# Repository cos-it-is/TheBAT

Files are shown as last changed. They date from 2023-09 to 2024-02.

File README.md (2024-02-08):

# Welcome to The B.A.T - A Bitcoin Lightning ATM! 

This repository contains the instructions for building and deploying your very own B.A.T Bitcoin Lightning ATM.

Support the project or buy one here: https://geyser.fund/project/thebatlightningatm or https://satsbat.com 🦇

Support me here: https://www.buymeacoffee.com/cutthepretence 🍺

Join the support group here: https://t.me/BitcoinAutoTeller

====



The B.A.T, short for Bitcoin Auto Teller directly integrates with https://lnbits.com as a funding wallet. 
It is the first highly functional Bitcoin Lightning ATM to incorporate NFC withdrawls that support LNURL, LN Address and [Boltcard](https://www.boltcard.org/ "Boltcard"). It has many features, including thermal printer, NFC withdrawl, and Over-The-Air (OTA) update capability, a large screen and enhanced user customisation options. The B.A.T is designed to sit in between a hobbyists dream and commercial environment.
It was born from a vision to creatly a very useable, small and portable ATM that can spark Bitcoin circular economies anywhere. 
It can be taken to events, markets, shops, parties. All you need is a power supply (plug or battery) and a wifi connection (for some options such as NFC).
It does however, work completely offline.
The ATM also functions as a straight paper Gift voucher dispenser, adding a completely secondary and unique function.



## Trademark

"The BAT" is a trademark. You are welcome to hack, fork, build, and use the source code and instructions found in this repository. However, the right to use the name "The BAT" or logo with any products or services is withheld and reserved for the trademark owner. Please be respectful and utilise your own logo/brand.

The BAT is based on the [FOSSA](https://github.com/lnbits/fossa "FOSSA") by Ben Arc.



====

# Components:

Before starting, please gather the following components that will be required for this project:

12V 3A DC adapter (Power Source) such as [THIS](https://www.ebay.co.uk/itm/225019408019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 "THIS")

12V DC adapter (Power Source) such as [THIS](https://www.ebay.co.uk/itm/225019408019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 "THIS")

12V/5V converter such as [THIS](https://www.ebay.co.uk/itm/193727621572 "THIS")

12V TTL Thermal Printer (You also need the USB to serial cable for uploading the Logo) [THIS](https://www.aliexpress.com/item/4001275848142.html?channel=twinner "THIS")

NV10 USB+ Note acceptor [THIS](https://www.innovative-technology.com/products/products-main/127-nv10-usb "THIS")

DG600F Coin acceptor [THIS](https://www.aliexpress.com/item/32951358676.html?channel=twinner "THIS")

ZX7D00CE01 7-inch screen with integrated ESP32-S3 (You also need the tool for burning) - [THIS](https://www.aliexpress.com/item/1005005000593458.html?spm=a2g0o.order_list.order_list_main.99.4f051802XMsYg2 "THIS")

Momentary 3.3v button (with a harness) such as [THIS](https://www.ebay.co.uk/itm/255737525408 "THIS")

Power 12v button (with a harness) such as [THIS](https://www.ebay.co.uk/itm/255737525408 "THIS")

5.5mm x 2.1mm Female Male DC Power Plug Adapter such as [THIS](https://www.aliexpress.com/item/32990194795.html?channel=twinner "THIS")

5.1mm X 2.1mm female power connector such as [THIS](https://www.aliexpress.com/item/1005003494724471.html?channel=twinner "THIS")

5.1 X 2.1mm Male to Female dual splitter such as [THIS](https://www.aliexpress.com/item/4000552846445.html?channel=twinner "THIS")

HW-307 Relay module or similar such as [THIS](https://www.ebay.co.uk/itm/225559844989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 "THIS")

Coin Acceptor LED Surround such as [THIS](https://www.aliexpress.com/item/1005002995360644.html?channel=twinner "THIS")

NV10 Host Cable - needed to change currency datasets or custom options on the acceptor [THIS](https://innovative-technology.com/shop/cables/nv9-nv10-usb-host-cable-detail "THIS") 

Coin Acceptor LED Surround such as [THIS](https://www.aliexpress.com/item/1005002995360644.html?channel=twinner  "THIS")

PN532 NFC Board (Set in I2C Mode using switches on board) such as [THIS](https://www.amazon.co.uk/HiLetgo-PN532-Module-Communication-Android/dp/B01I1J17LC  "THIS")

====

## Programming the Thermal Printer:

Start by downloading the printer setting software available [THIS](https://www.hsprinter.com/?m=common&a=down&name=639a91a94e329.zip&g=e "THIS") .

• First, you need to ensure that the printer is set to a 19200 baud rate.

• Now, open the printer setting software and navigate to the "Upload" section.

• Select your own printer_logo.bmp file for upload. This should be in greyscale and around 270x270 pixels.

• Proceed to upload the "printer_logo.bmp" file to your thermal printer.

Remember, it is crucial to use the precisely labeled "printer_logo.bmp" file and to set the printer to the 19200 baud rate for successful functioning.

## Programming The DG600F Coin Acceptor:

• Start by holding down the "A" button. Keep it pressed.

• While still pressing the "A" button, press the "A" button again and then hit the "B" button. Do this for the specific coin you want to program (for instance, 5p).

• Continue pressing the buttons for the designated coin until you hear a beep. This usually happens after 20 presses. For accuracy, it is best to use a variety of the same coin.

• Repeat steps 1-3 for all six coins that you want to program.

• Now, press and hold the "B" button, then press the "A" button to switch to the A2 setting. If not sure, the default setting is A1.

• Follow this configuration: Set A2 to 02. Set A3, A4, and A5 to 01.

• Finally, press and hold the "A" button to exit the programming mode.

There are instructions in the manual and many youtube videos of this process available.

## Programming the NV10 USB+ Note Acceptor:

• Download the Validator Manager and Drivers suitable for your specific currency from the Innovative Technologies website (Create a free account).

• Install and plug the cable of the NV10 USB+ into your PC using the host cable cable for programming

• Navigate to your device manager and ensure that your PC detects the connected NV10 USB+ using the instructions in the manual.

• Next, open the Validator Manager software and locate the programming option. Select it.

• In this section, choose the 'bv1' file to program the device.

• Modify the user mode to 'advanced' setting for additional features.

• In the interface section, set the parameter to 'SIO'.

• Now, enable the 'Credit card rejection' option to ensure the machine doesn't process invalid entries.

• Once all changes are completed, ensure to save and apply these new parameters.

## Programming the 7-inch Screen with Integrated ESP32S3 using Arduino:

• Begin by launching your Arduino IDE.

• Connect integrated screen to your PC and install relevant drivers and arduino libraries.

• Navigate to the 'Tools' tab on the menu bar.

• In the dropdown menu, select the options as shown in the image provided:



Alternatively, use a buring tool and the .BIN file provided in releases to install the firmware.

# How to build:
• Connect the devices together as per the wiring diagram. You can use Dupont wires or for the board, you can use a 2x40 (40 pin) IDC connector to breakout the pins. This is a 2mm pitch (not common 2.54mm)

| Terminal Pin | GPIO | Description |
|---|---|---|
| 26 | 40 | Note TXB |
| 27 | 4 | Printer TXP |
| 29 | 1 | Button |
| 23 | 20 | Coin Inhibit |
| 25 | 41 | Note RXB |
| 28 | 42 | Printer RXP |
| 24 | 19 | Coin RXC |
| 30 | 2 | Relay |
| 31 | 47 | NFC - SCL |
| 32 | 48 | NFC - SDA |
| 2 | N/A  | Relay 5v |
| 6 | N/A  | Relay GND |
| 3 | N/A  | Button 3v |
| 5 | N/A  | Button GND |
| 1 | N/A  | NFC 5v |

# How to use:

## Booting into Configuration Mode:
When you want to configure your B.A.T. device, you'll need to launch the access point. To do this, press the boot button on the burner cable during boot. The access point will have a name similar to "The B.A.T - {mac address}".

Once you've connected to the access point, you can begin setting up the device.

This can sometimes be an issue when using OTA updates. It is best (on android at least) I have found using edge browser to perform OTA updates.

## Configuration Options:

Network and wallet configuration, You can change several parameters:

## General Options:

- Access point password: Choose a password to secure your device's access point. Detault is 'thebatatm'
- LNURLDevice string: Set the connection string for funding. This can be from lnbits.com or self-hosted.
- Live rate API URL: Set an API endpoint for retrieving live rates. e.g., https://legend.lnbits.com/lnurlp/api/v1/rate/GBP.
- Wallet endpoint URL: Set the endpoint URL for wallet actions. e.g., https://legend.lnbits.com/api/v1/wallet.
- API Key: Input your API Key, such as 69f5a4afe7834ddsj3jd7dj4f44cd82.
- Screen Brightness: Set to High, Medium or Low.

## Acceptor and Fiat Settings:

- Enable or disable accepting notes or coins.
- Set coin and bill values for the acceptors.
- Set a maximum deposit value for each transaction.
- Set a fee rate.
- You can set a redemption period for each transaction when the thermal printer is in use.

## Custom Options:

- Turn off/on the LED surround for the coin acceptor.
- Enable/disable displaying the live rate. (Wifi connection required)
- Set a balance check after each transaction. (Wifi connection required)

## Withdrawl Settings:
- Set the output display options of the transaction QR codes – it could be the screen, print, or both.
- You can decide to display Bitcoin quotes or jokes on each receipt – it would be selected randomly each time.
- You can set a URL of your website or LNBits install URL (And other information you like) that prints on the receipt for promotional purposes.
- The maximum number of receipts that can be printed on the thermal printer can be set.
- Set in ATM or Gift voucher modes. ATM acts like an ATM, but Gift voucher acts like a voucher dispenser, printing to receipt only and adding different information to the receipt.
- Enable/Disable NFC withdrawls. (Wifi connection required)
- Withdrawl period timeout for transaction (with backup receipt printing if needed)

## Network Time Protovol (NTP) Settings:

- Configure your timezone, NTP server, and sync intervals for accurate timestamps on printed receipts. (Wifi connection required)
- A time offset can be set for regions observing daylight saving.

## Display Settings:

- Change screen brightness
- Set the color mode of your display: default grafitti, stealth black and white, or set your custom color options.

## Translation Settings:

- Set the default and second language (with string translations) for your device. A button press when the ATM is in use will change the language.

## Updating Firmware:
- The B.A.T device allows firmware updates via OTA using .BIN files. To apply a new firmware update, navigate to the Update section in the access point, and proceed to flash the new release of the firmware.

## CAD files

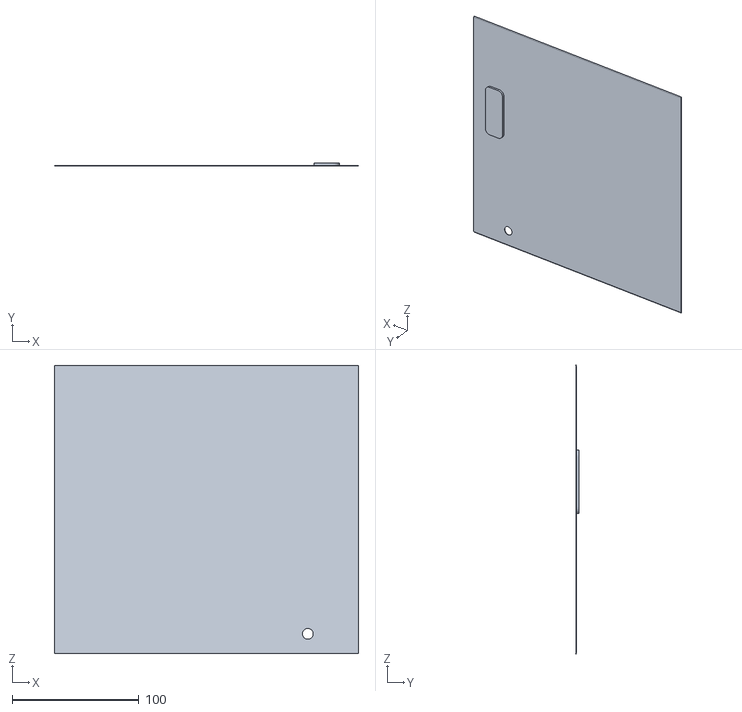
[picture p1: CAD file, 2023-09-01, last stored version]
3D Print Cases/Block/Block Door.stl
240.0 x 2.47 x 227.6

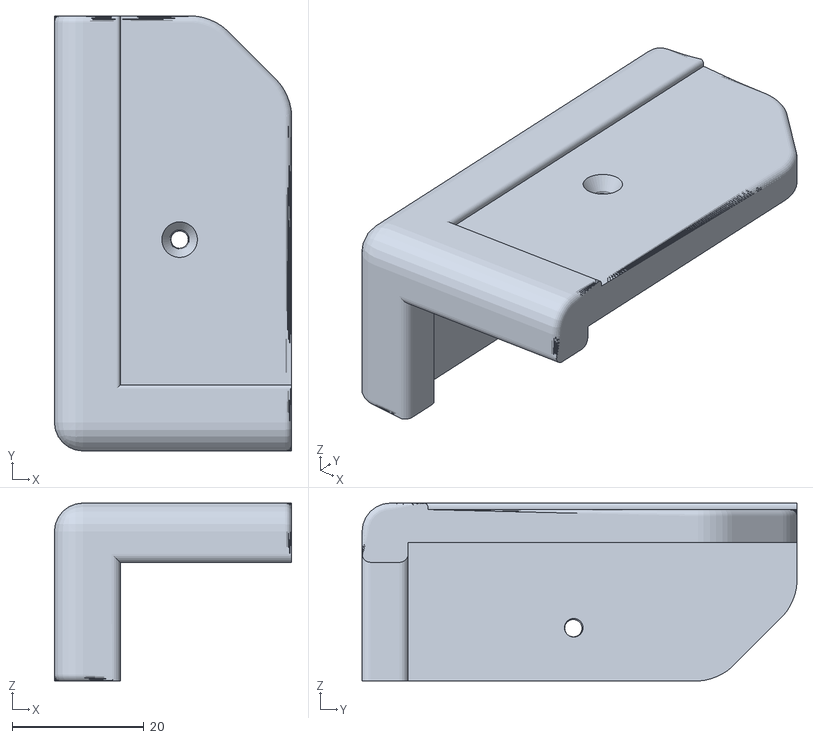
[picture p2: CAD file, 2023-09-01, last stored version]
3D Print Cases/Common/R corner.stl
36.0 x 66.0 x 27.0

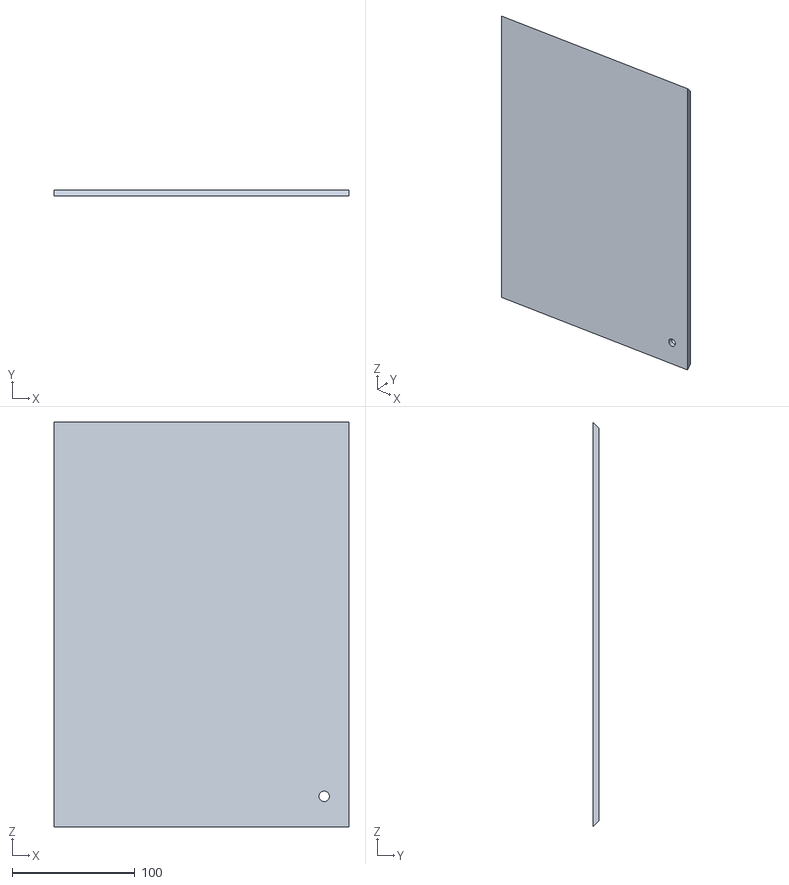
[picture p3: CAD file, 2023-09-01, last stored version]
3D Print Cases/Moon/Moon Door.stl
240.0 x 5.00 x 330.0

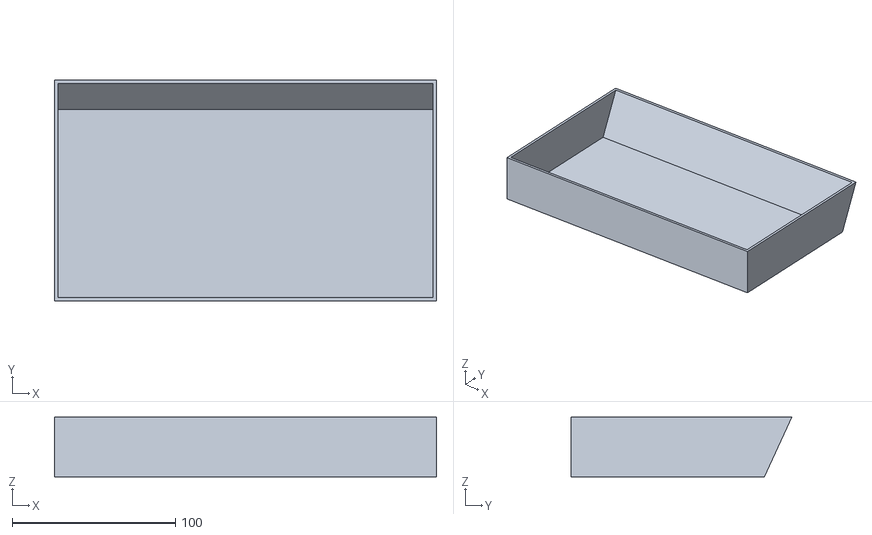
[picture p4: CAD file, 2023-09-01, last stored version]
3D Print Cases/Block/Block Tray.stl
234.0 x 135.2 x 36.5

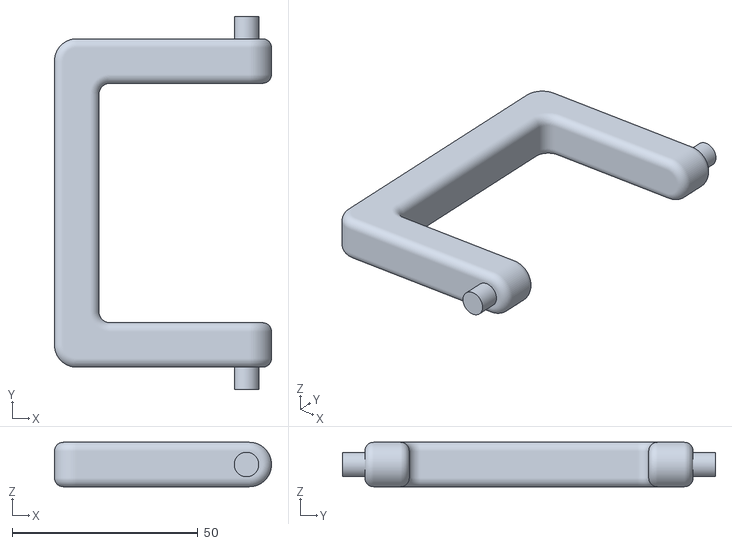
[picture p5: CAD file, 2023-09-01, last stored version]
3D Print Cases/Common/Handle.stl
58.5 x 100.5 x 12.0

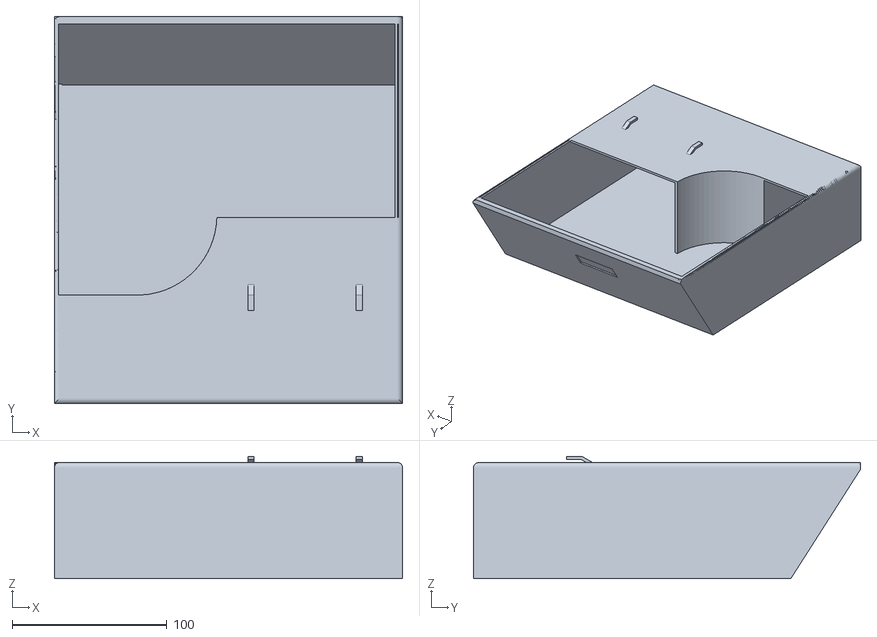
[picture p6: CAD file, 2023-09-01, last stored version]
3D Print Cases/Moon/Moon Tray.stl
225.0 x 250.0 x 79.0

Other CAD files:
3D Print Cases/Common/L corner.stl

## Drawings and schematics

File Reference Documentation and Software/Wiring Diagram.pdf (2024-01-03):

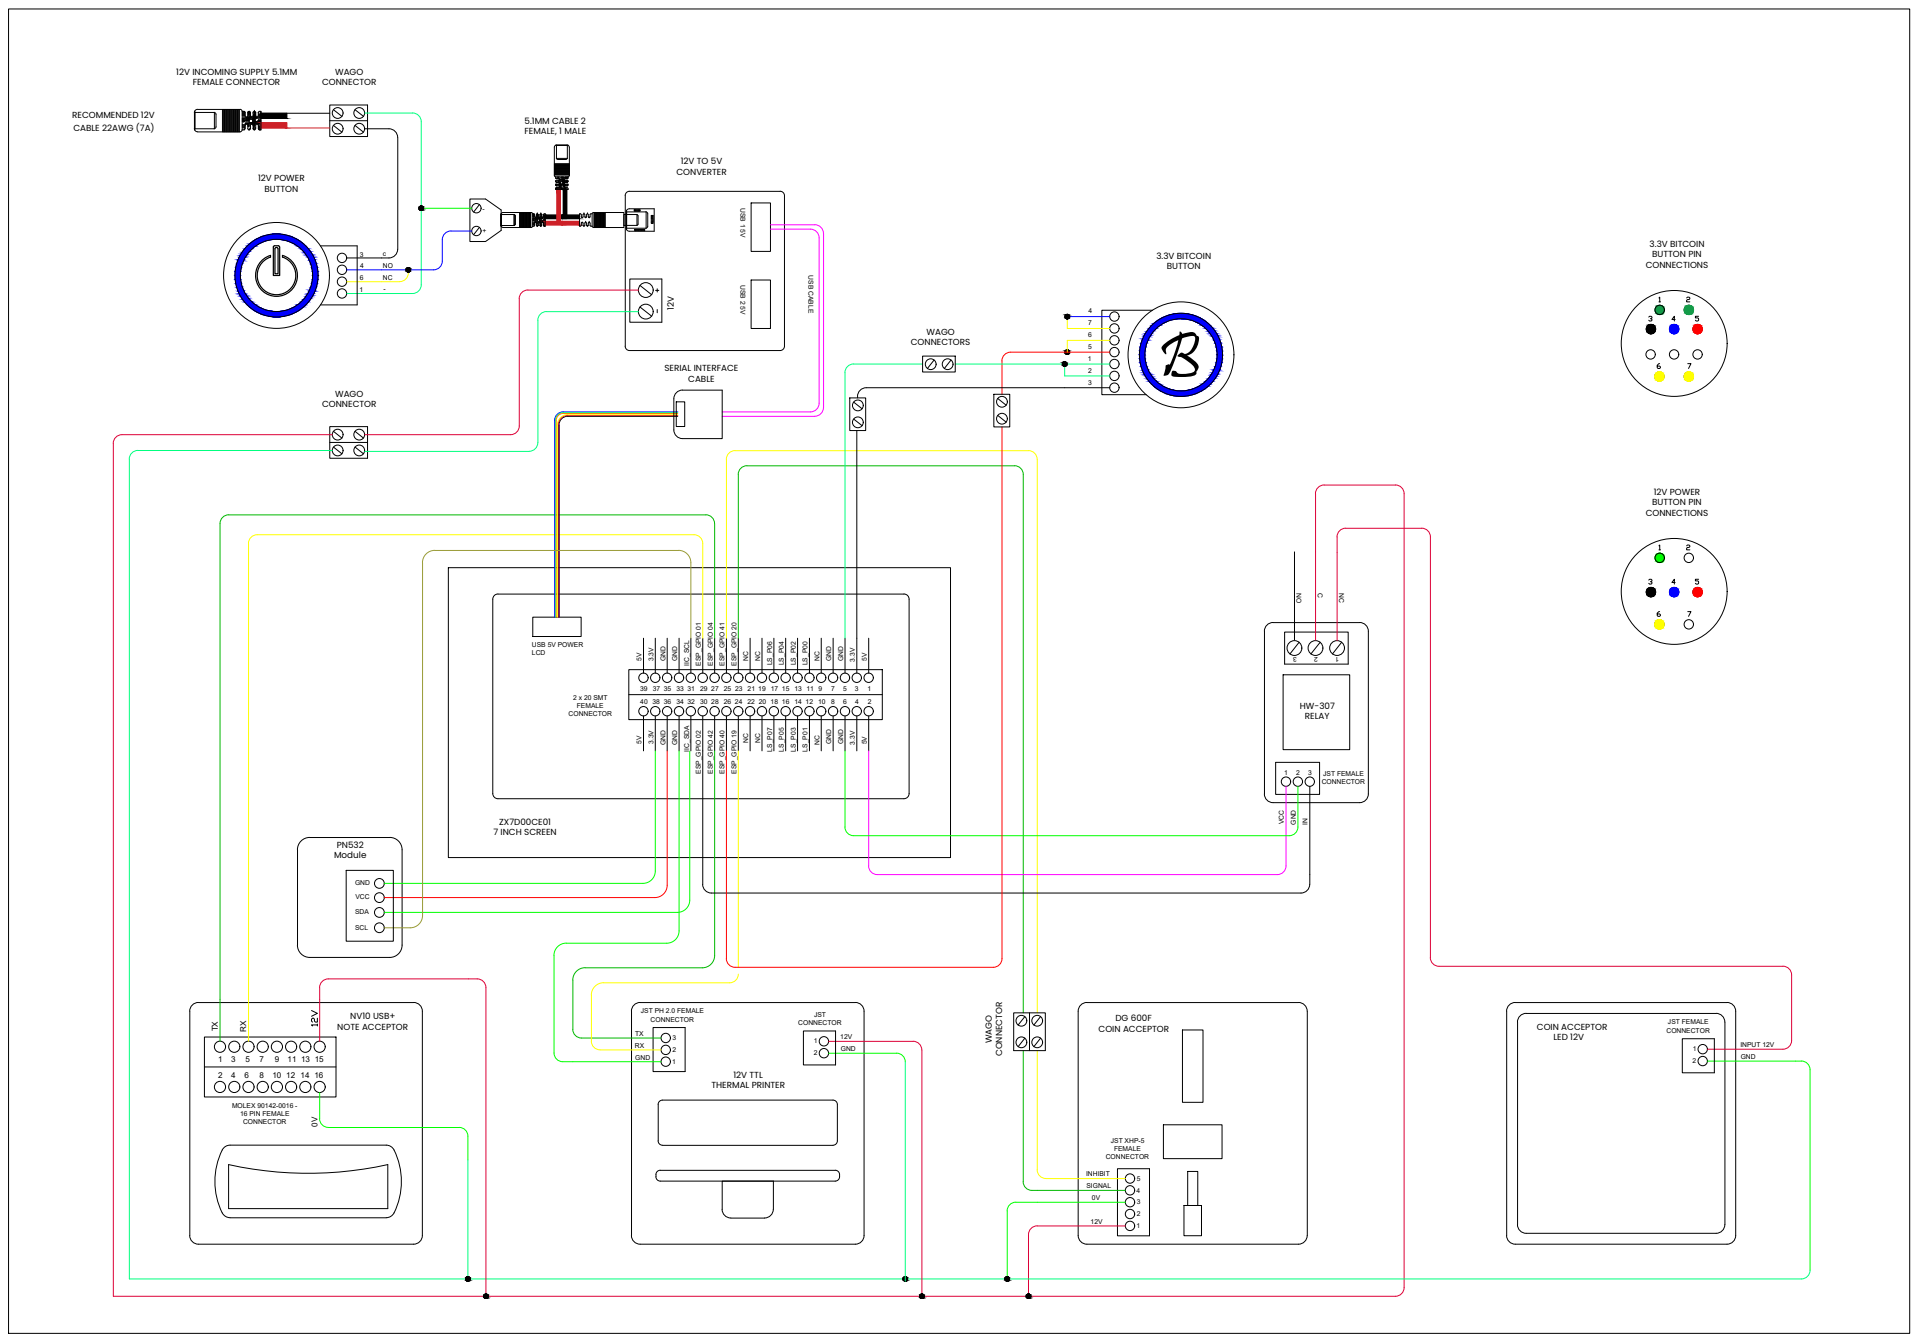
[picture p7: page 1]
ZX7D00CE01 7 INCH SCREEN; 3.3V GND GND; IIC_SCL ESP_GPIO 01 ESP_GPIO 04 ESP_GPIO 41 ESP_GPIO 20; LS_P00 NCGND GND; ESP_GPIO 02 ESP_GPIO 42 ESP_GPIO 40 ESP_GPIO 19; LS_P01 NCGND GND; VCC GND

NC HW-307 RELAY 12V POWER BUTTON COIN ACCEPTOR LED 12V INPUT 12V GND 12 12V TO 5V CONVERTER 12V INCOMING SUPPLY 5.1MM FEMALE CONNECTOR

12V WAGO CONNECTOR +- WAGO CONNECTOR USB 5V POWER LCD JST PH 2.0 FEMALE CONNECTOR JST CONNECTOR JST XHP-5 FEMALE CONNECTOR JST FEMALE CONNECTOR JST FEMALE CONNECTOR MOLEX 90142-0016 - 16 PIN FEMALE CONNECTOR 2 x 20 SMT FEMALE CONNECTOR SERIAL INTERFACE CABLE

CONNECTOR RECOMMENDED 12V CABLE 22AWG (7A) GND VCC SDA SCL PN532 Module

USB CABLE WAGO CONNECTORS 5.1MM CABLE 2 FEMALE, 1 MALE 3.3V BITCOIN BUTTON PIN CONNECTIONS 12V POWER BUTTON PIN CONNECTIONS 4765123 3461

USB 1 5V USB 2 5V B3.3V BITCOIN BUTTON

NC cNONC- DG 600F COIN ACCEPTOR INHIBIT SIGNAL 0V12V 54321 NV10 USB+ NOTE ACCEPTOR 1615 1413 12 1 3 5 7 9 11 2 4 6 8 10

0V 12V TTL THERMAL PRINTER TXRXGND 321 12V GND 12

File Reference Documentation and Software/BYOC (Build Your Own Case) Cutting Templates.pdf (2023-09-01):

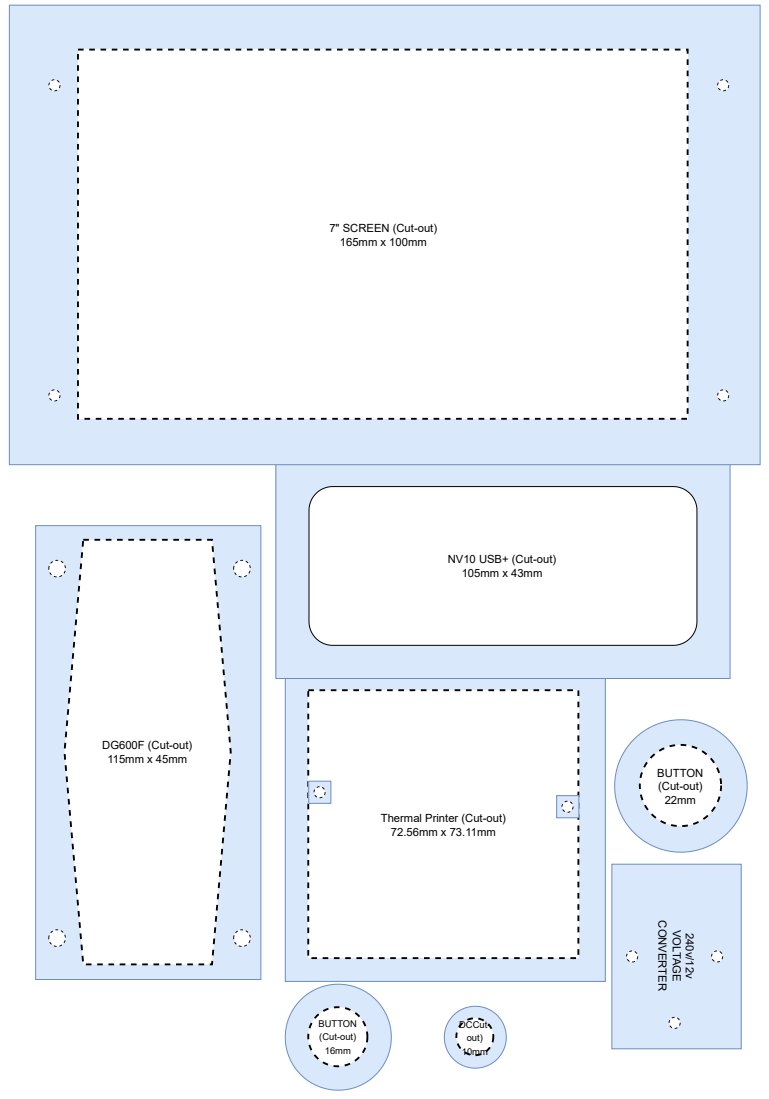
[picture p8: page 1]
DG600F (Cut-out) 115mm x 45mm; BUTTON (Cut-out) 16mm; DCCut- out) 10mm; BUTTON (Cut-out) 22mm; VOL; TAGE; CONVERTER

7" SCREEN (Cut-out)

NV10 USB+ (Cut-out)

Thermal Printer (Cut-out)

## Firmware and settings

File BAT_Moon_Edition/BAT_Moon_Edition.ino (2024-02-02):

#include <HTTPClient.h>
#include <WiFi.h>
#include <WebServer.h>
typedef WebServer WiFiWebServer;
#include <FS.h>
#include <SPIFFS.h>
#include <AutoConnect.h>
#include <Wire.h>
#include <HardwareSerial.h>
#include <ArduinoJson.h>
#include <JC_Button.h>
#include <cmath>
#include <Hash.h>
#include "qrcoded.h"
#include "Bitcoin.h"
#include <U8g2lib.h>
#include <Arduino_GFX_Library.h>
#include <Adafruit_Thermal.h>
#include <stdlib.h>
#include "time.h"
#include "logo.h"  //logo images
#include <ctype.h>
#include <WebSocketsClient.h>
#include <Hash.h>
#include "Adafruit_AW9523.h"
#include <Adafruit_PN532_NTAG424.h>
#include <PN532_I2C.h>
#include <PN532.h>


//========================================================//
//===================HARDWARE SETTINGS====================//
//========================================================//

//SETUP SCREEN - 7 INCH
#define GRAFFITI 0xFFFF
#define TFT_BL 45

Arduino_ESP32RGBPanel* rgbpanel = new Arduino_ESP32RGBPanel(
  39 /* DE */, 38 /* VSYNC */, 5 /* HSYNC */, 9 /* PCLK */,
  10 /* R0 */, 11 /* R1 */, 12 /* R2 */, 13 /* R3 */, 14 /* R4 */,
  21 /* G0 */, 0 /* G1 */, 46 /* G2 */, 3 /* G3 */, 8 /* G4 */, 18 /* G5 */,
  17 /* B0 */, 16 /* B1 */, 15 /* B2 */, 7 /* B3 */, 6 /* B4 */,
  0 /* hsync_polarity */, 0 /* hsync_front_porch */, 210 /* hsync_pulse_width */, 30 /* hsync_back_porch */,
  0 /* vsync_polarity */, 0 /* vsync_front_porch */, 22 /* vsync_pulse_width */, 13 /* vsync_back_porch */,
  1 /* pclk_active_neg */, 16000000 /* prefer_speed */,
  0 /* de_idle_high */, 0 /* pclk_idle_high */, true /* auto flush*/);

Arduino_RGB_Display* gfx = new Arduino_RGB_Display(
  800 /* width */, 481 /* height */, rgbpanel, 2 /* rotation */);

//FORMATTING
bool format = false;  // true for formatting memory, use once, then make false and reflash

//BUTTON SETTINGS
#define buttonPin 1  //Set to GPIO for signal to button, only works on some GPIO. Don't change
int debounce = 25;   //Set the debounce time (milliseconds) for the button, default should be 25, but may need modification if issues with sporadic presses are seen.
#define apButton 0

//BILL ACCEPTOR SETTINGS
#define RXB 41  //define the GPIO connected TO the TX of the bill acceptor
#define TXB 40  //define the GPIO connected TO the RX of the bill acceptor

//COIN ACCEPTOR SETTINGS
#define RXC 19          //define the GPIO connected TO the SIGNAL/TX of the coin acceptor
#define INHIBITMECH 20  //define the GPIO connected TO the INHIBIT of the coin acceptor

//THERMAL PRINTER SETTINGS
#define RXP 42  //define the GPIO connected TO the TX of the thermal printer
#define TXP 4   //define the GPIO connected TO the RX of the thermal printer

//RELAY SETTINGS--
#define RELAY_PIN 2

//NFC PN532
#define I2C_SDA 48
#define I2C_SCL 47


struct Quote {
  String text;
  String author;
};

Quote quotes[] = {
  { "The root problem with conventional currency is all the trust that's required to make it work.", "Satoshi Nakamoto" },
  { "Bitcoin is a remarkable cryptographic achievement and the ability to create something that is not duplicable in the digital world has enormous value.", "Eric Schmidt" },
  { "I do think Bitcoin is the first [encrypted money] that has the potential to do something like change the world.", "Peter Thiel" },
  { "The more commodity use cases we have for Bitcoin, the better money it becomes. Think of Gold.", "Ben Arc" },
  { "Bitcoin will do to banks what email did to the postal industry.", "Rick Falkvinge" },
  { "With e-currency based on cryptographic proof, without the need to trust a third-party middleman, money can be secure and transactions effortless.", "Satoshi Nakamoto" },
  { "Bitcoin may be the TCP/IP of money.", "Paul Buchheit" },
  { "If we remember, 15 years ago if you were doing anything on the internet you were going to make millions. I think it could be the same with Bitcoin.", "Jared Kenna" },
  { "Bitcoin is a very exciting development, it might lead to a world currency.", "Kim Dotcom" },
  { "Bitcoin actually has the balance and incentives right, and that is why it is starting to take off.", "Julian Assange" },
  { "So bitcoin is cyber snob currency...", "William Shatner" },
  { "Virgin Galactic is a bold entrepreneurial technology. It's driving a revolution and Bitcoin is doing just the same when it comes to inventing a new currency.", "Sir Richard Branson" },
  { "I really like Bitcoin. I own Bitcoins. It's a store of value, a distributed ledger. It's a great place to put assets, especially in places like Argentina with 40 percent inflation, where $1 today is worth 60 cents in a year, and a government's currency does not hold value.", "David Marcus" },
  { "I am very intrigued by Bitcoin. It has all the signs. Paradigm shift, hackers love it, yet it's derided as a toy. Just like microcomputers.", "Paul Graham" },
  { "Bitcoin is money 2.0, a huge huge huge deal.", "Chamath Palihapitiya" },
  { "You can't stop things like Bitcoin. It will be everywhere and the world will have to readjust. World governments will have to readjust.", "John McAfee" },
  { "Bitcoin is here to stay.", "Roger Ver" },
  { "Bitcoin seems to be a very promising idea. I like the idea of basing security on the assumption that the CPU power of honest participants outweighs that of the attacker.", "Hal Finney" },
  { "Blockchain is the tech. Bitcoin is merely the first mainstream manifestation of its potential.", "Marc Kenigsberg" },
  { "Bitcoin is a very exciting development, it might lead to a world currency. I think over the next decade it will grow to become one of the most important ways to pay for things and transfer assets.", "Kim Dotcom" }
};

struct Joke {
  String text;
};

Joke jokes[] = {
  { "Why don't Bitcoin holders have a panic room? Because there's no room for panic when you HODL." },
  { "Why was the computer cold? It left its Windows open for Bitcoin mining." },
  { "Why couldn't the Bitcoin blockchain buy a house? It couldn't afford the high 'fees'." },
  { "Why do Bitcoiners want a Lamborghini? Because it's the only car that increases in value faster than their Bitcoin." },
  { "What's the difference between Bitcoin and Las Vegas? What happens in Bitcoin stays on the blockchain." },
  { "Why are Bitcoiners immune to inflation? They take a 'byte' out of it every day." },
  { "Why was the Bitcoiner excited at their birthday party? He thought the candles on the cake were a bullish signal." },
  { "Why don't Bitcoin traders ever sleep? Because they fear they'll wake up to a market crash." },
  { "Why was the computer that was mining Bitcoin happy? It was racking up a lot of 'byte' points." },
  { "Why are Bitcoiners excited about late nights? Because the moon is closer." }
};


//GENERAL SETTINGS--
String fwVersion = "2.1";  //set the version of the firmware release here.
String hwVersion = "2.1";  //set the version of the hardware release here.
#define MAX_DATA_SIZE 854  // maximum allowed size of NFC data
#define AW9523_ADDRESS 0x5B

//========================================================//
//========================================================//
//========================================================//


///////////////////////////////////////////////
////////OTHER VARIABLES AND DECLARATIONS///////
///////////////////////////////////////////////

bool paymentVerified = false, paymentFailed = false, lowBalance = false, isBoltcard = false, nativeLang, dualLang, stealthMode, ledOn, liveRate, useGraffiti, acceptCoins, acceptNotes, coinOnly, enableWifi, enableNfc, atmMode, giftMode, thermalQR, screenQR, printQuotes, printJokes, triggerAp = false, backupReceipt, balanceCheck, wsDataReceived = false, pauseScanning = false;
uint16_t colour1, colour2, colour3, colour4, colour5, background;
uint8_t metadataHash[32];
String lannN = "", lauN = "", porN = "", resN = "", staN = "", wakN = "", entN = "", buyN = "", bitN = "", herN = "", insN = "", exiN = "", lanN = "", feeN = "", totN = "", scaN = "", indN = "", recN = "", scaQRN = "", valN = "", dayN = "", daysN = "", enjN = "", errN = "", errQRN = "", CountdownN = "", timerExpN = "", walletN = "", conN = "", nfcdN = "", nfc1N = "", nfc2N = "", nfc3N = "", nfc4N = "", nfc5N = "", procN = "", recwalN = "", giftvN = "", lnaN = "", maxaN = "", walbalN = "", paidN = "";
String lannE = "English", porE = "Access Point Launched.", resE = "Restart and launch Access Point to Configure", buyE = "BUY", bitE = "BITCOIN", herE = "HERE", insE = "Insert cash to buy Bitcoin", exiE = "Press button to finish", feeE = "Fee", lanE = "Press button to change language", totE = "Total", scaE = "Scan to receive sats.", walletE = "Funding wallet is low, please top-up and restart.";
String indE = "Inserted", recE = "Please take your receipt.", scaQRE = "Scan this QR code with a lightning wallet to receive your sats!", valE = "This is valid for", dayE = "day only", daysE = "days only", enjE = "Enjoy your Sats!", errE = "Error Printing: Check Printer", errQRE = "QR Code will shortly be displayed on the screen.", CountdownE = "Time Remaining", timerExpE = "Timer expired! Printing instead.";
String conE = "Please contact operator via", nfc1E = "NFC Disabled", nfc2E = "Press button for QR", nfc3E = "Failed, retry or scan QR.", nfc4E = "Please scan QR instead.", nfc5E = "Or tap NFC below.", procE = "Processing. Please Wait.", recwalE = "Recommended wallet", giftvE = "Gift Voucher", lnaE = "LNURL-LN Address or BoltCard", maxaE = "Max Amount", paidE = "PAID", walbalE = "Wallet Balance";
String lann, por, res, ver, buy, bit, her, ins, exi, lan, fee, tot, sca, ind, rec, scaQR, val, day, days, enj, err, errQR, Countdown, timerExp, wallet, con, email, nfc1, nfc2, nfc3, nfc4, nfc5, proc, recwal, giftv, lna, maxa, paid, walbal, qrData, ssid, apPassword = "thebatatm", wifiPassword, lnurlATM, baseURLATM, secretATM, currencyATM = "", ntpServer, invoice, walletServer, walletID, coinValues, billValues, tz, url, lnurlp, adminKey, decodeUrl, metadata, domain, callback, hashString;
String laddrUrl = "", lnurl = "", nfcData = "", receivedData = "", recWallet = "";
int maxAmount, charge, bills, moneyTimer, converted, redemptionPd, timer = 0, screenW = 800, screenH = 480, maxReceipts;
float coins, total;
int billAmountInt[6];
float coinAmountFloat[6];
float coinAmountSize = sizeof(coinAmountFloat) / sizeof(float);
int billAmountSize = sizeof(billAmountInt) / sizeof(int);
int brightness = 200;
double exchangeRateSAT = -1, exchangeRateCUR = -1;
long gmtOffset_sec = 0;
struct tm timeinfo;
char lnurlData[MAX_DATA_SIZE], laddrData[MAX_DATA_SIZE];
unsigned long maxAmountInSats, balanceInSats;

// Store the last NTP time in a timestamp
time_t lastSyncNtpTime = 0;
unsigned long lastSyncTimeSec = 0, syncInterval, timerDuration, getRateInterval;


fs::SPIFFSFS& FlashFS = SPIFFS;
#define FORMAT_ON_FAIL true
#define ELEMENTS_FILE "/elements.json"
#define LANGUAGE_FILE "/language.json"
JsonObject obj;

struct LookupTable {
  char character;
  byte value;
};

LookupTable PC437Characters[] = {
  { 'Ç', 0x80 }, { 'ü', 0x81 }, { 'é', 0x82 }, { 'â', 0x83 }, { 'ä', 0x84 }, { 'à', 0x85 }, { 'å', 0x86 }, { 'ç', 0x87 }, { 'ê', 0x88 }, { 'ë', 0x89 }, { 'è', 0x8A }, { 'ï', 0x8B }, { 'î', 0x8C }, { 'ì', 0x8D }, { 'Ä', 0x8E }, { 'Å', 0x8F }, { 'É', 0x90 }, { 'æ', 0x91 }, { 'Æ', 0x92 }, { 'ô', 0x93 }, { 'ö', 0x94 }, { 'ò', 0x95 }, { 'û', 0x96 }, { 'ù', 0x97 }, { 'ÿ', 0x98 }, { 'Ö', 0x99 }, { 'Ü', 0x9A }, { '¢', 0x9B }, { '£', 0x9C }, { '¥', 0x9D }, { '₧', 0x9E }, { 'ƒ', 0x9F }, { 'á', 0xA0 }, { 'í', 0xA1 }, { 'ó', 0xA2 }, { 'ú', 0xA3 }, { 'ñ', 0xA4 }, { 'Ñ', 0xA5 }, { 'ª', 0xA6 }, { 'º', 0xA7 }, { '¿', 0xA8 }, { '⌐', 0xA9 }, { '¬', 0xAA }, { '½', 0xAB }, { '¼', 0xAC }, { '¡', 0xAD }, { '«', 0xAE }, { '»', 0xAF }, { 'α', 0xE0 }, { 'ß', 0xE1 }, { 'Γ', 0xE2 }, { 'π', 0xE3 }, { 'Σ', 0xE4 }, { 'σ', 0xE5 }, { 'µ', 0xE6 }, { 'τ', 0xE7 }, { 'Φ', 0xE8 }, { 'Θ', 0xE9 }, { 'Ω', 0xEA }, { 'δ', 0xEB }, { '∞', 0xEC }, { 'φ', 0xED }, { 'ε', 0xEE }, { '∩', 0xEF }, { '≡', 0xF0 }, { '±', 0xF1 }, { '≥', 0xF2 }, { '≤', 0xF3 }, { '⌠', 0xF4 }, { '⌡', 0xF5 }, { '÷', 0xF6 }, { '≈', 0xF7 }, { '°', 0xF8 }, { '∙', 0xF9 }, { '·', 0xFA }, { '√', 0xFB }, { 'ⁿ', 0xFC }, { '²', 0xFD }
};

// Function to lookup byte value of a character in CodePage437
byte lookup(char character) {
  for (unsigned int i = 0; i < sizeof(PC437Characters) / sizeof(LookupTable); i++) {
    if (PC437Characters[i].character == character) {
      return PC437Characters[i].value;
    }
  }

  // Return a default value if character is not found in the lookup table
  return 0x00;
}
/////////////////////////////////////////
////END OF VARIABLES AND DECLARATIONS////m
/////////////////////////////////////////
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
void loop() {

  gfx->fillScreen(background);
  webSocket.loop();
  moneyTimerFun();
  getDatetime();
  makeLNURL();
  checkForError();
  bool isError = checkForError();



  if (screenQR && !thermalQR) {
    qrShowCodeLNURL();
  }

  if (thermalQR && !screenQR) {
    if (isError) {
      gfx->fillScreen(WHITE);
      printText(err.c_str(), u8g2_font_helvB18_te, 2, RED, false, -1, 80);
      printText(errQR.c_str(), u8g2_font_helvB18_te, 1, RED, false, -1, 200);
      delay(5000);
      qrShowCodeLNURL();
    } else {
      gfx->fillScreen(WHITE);
      printText(rec.c_str(), u8g2_font_helvB18_te, 2, colour4, false, -1, -1);
      if (atmMode) {
        printReceipt(qrData);
      } else {
        printVoucher(qrData, recWallet);
      }
      delay(5000);
      receiptCounter();
    }
  }

  if (screenQR && thermalQR) {
    if (isError) {
      gfx->fillScreen(WHITE);
      printText(err.c_str(), u8g2_font_helvB18_te, 2, RED, false, -1, 80);
      printText(errQR.c_str(), u8g2_font_helvB18_te, 1, RED, false, -1, 200);
      delay(5000);
      qrShowCodeLNURL();
    } else {
      if (atmMode) {
        printReceipt(qrData);
      } else {
        printVoucher(qrData, recWallet);
      }
      delay(500);
      qrShowCodeLNURL();
      receiptCounter();
    }
  }
  // check machines
  if (acceptCoins) {
    digitalWrite(INHIBITMECH, HIGH);
  } else {
    digitalWrite(INHIBITMECH, LOW);
  }
  if (acceptNotes) {
    nSerial.write(184);
  } else {
    nSerial.write(185);
  }
}

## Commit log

2023-09-01 Added editions and build files
    Added 2 editions (Moon and Block) for note/thermal or just coin acceptor. Also, added wiring diagrams and 3D print files.
    [Block Door.stl, Block Tray.stl, Handle.stl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]
2023-09-01 Added Build Your Own Case Templates
2024-01-03 V2 NFC Enabled
    Added NFC withdrawals, bug fixes, screen brightness, and gift voucher modes.
    [Block Door.stl, Block Tray.stl, Handle.stl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]
2024-01-29 2.1
    Various fixes and improvements
    [BAT_Moon_Edition.ino]
2024-01-30 Version 2.1
    Fixes and setting NFC RF power to max.
    [BAT_Moon_Edition.ino]
2024-02-02 Tidy up
    [default_8MB.csv]
